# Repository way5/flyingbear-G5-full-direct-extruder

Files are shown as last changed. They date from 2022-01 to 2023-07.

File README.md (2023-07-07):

# FlyingBear Ghost 5: Direct Extruder
| WARNING | The project requires a minimal skills in electronics. Everything you do hereinafter is at your own risk. :) |
|:---:|:---|
| disclaimer | **Please refer to [issues](https://github.com/way5/flyingbear-G5-full-direct-extruder/issues) :beetle: if you have any suggestion or found an error.** |

## **+ Description**

**BOM:**

1. Carrige:
   -  BMG feeder by Mellow Store (right) - 1 pcs.
   -  NEMA17HS4023 motor - 1 pcs.
   -  Bolt M3 - 5 pcs.
   -  Nut M3 - 4 pcs.
   -  Screw M2 (PCB) - 3 pcs.
   -  Thru Threaded Inserts M3 - 5 pcs.
   -  Threaded Stud Bolt M3 - 4 pcs.
2. Y-axis Limit Switch:
   -  Bolt + Nut + Washer M2 - 1 pcs.
   -  Thru Threaded Insert M2 - 1 pcs.
   -  Any suitable Coil Spring (see photos) - 1 pcs.
3. Z-axis knob:
   - Bolt + Nut M3 - 1 pcs.
<br/>Optional:
   - Replacement coil spring (~5mm shorter than the stock one) - 1 pcs.
4. PCB:
   -  SMD LED diode - 1 pcs.
   -  SMD Resistor ≥ 1kOhm - 1 pcs.
   -  SMD Capacitor ~ 10nF - 1 pcs.
   -  Header Male 2x1 pins - 6 pcs.
   -  Header Male 7x2 pins - 1 pcs.

I'd recommend PETG or ABS plastic for all the printed parts. Keep in mind that it will be exposed to high heat near the hotend, espetially if you are using heated chamber on your printer.

The list of the parts you'd neet to print:

- Carrige
- Carrige Belt Clip
- Nozzle
- Y-axis Shaft Base + Pin Head
- Z-axis Nut + Nut Cap
- Back side cap for extruder motor insert

In case if you have installed heated chamber I strongly recommend you to prevent extruder motor overheat by using heatsinks and a cooling fan. I am using 30x30mm turbine that is attached to the carrige through the [extruder motor shroud](./OBJ/EXTRUDER%20MOTOR%20SHROUD.obj). See the corresponding 3d model.

Your new hotend carrige would look like this:

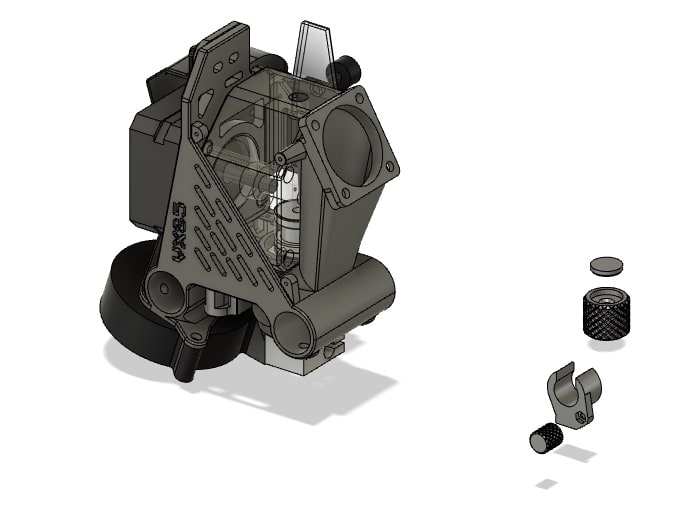
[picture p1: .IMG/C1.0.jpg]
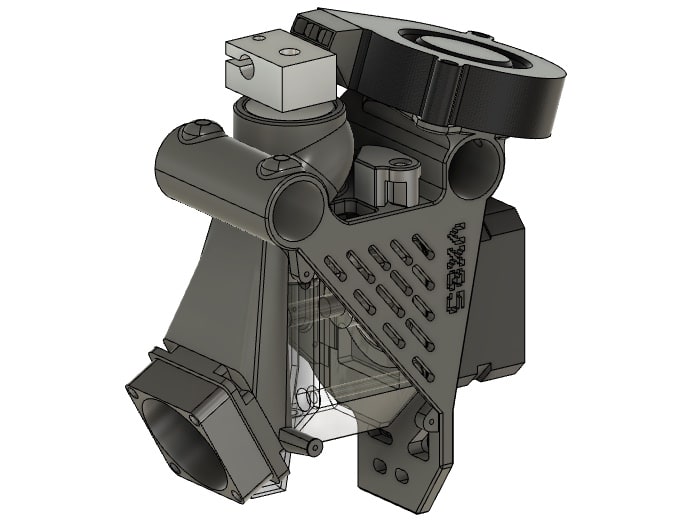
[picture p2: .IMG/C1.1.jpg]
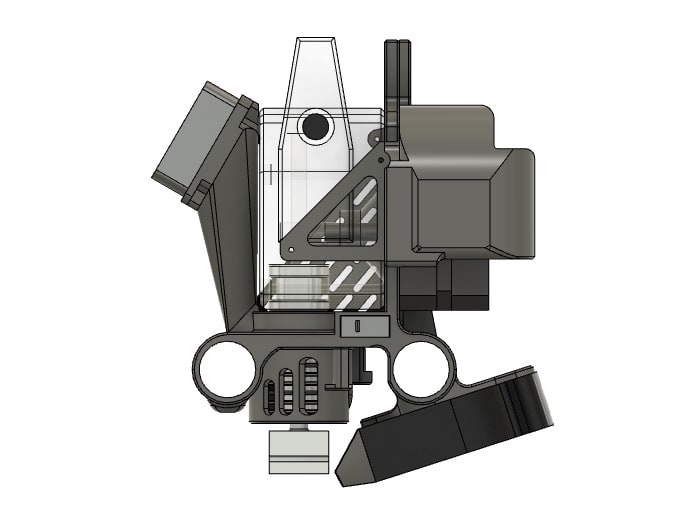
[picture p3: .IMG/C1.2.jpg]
||||
| --- | --- | --- |

For the extruder heatsink cooling being used stock Flyingbear's 30x30mm fan that is electrically connected (in parallel) to the same female pin header with extruder motor fan. Hotend cooling fan sits on the top of the air duct sleeve and blows downwards to the heatsink, see image below.

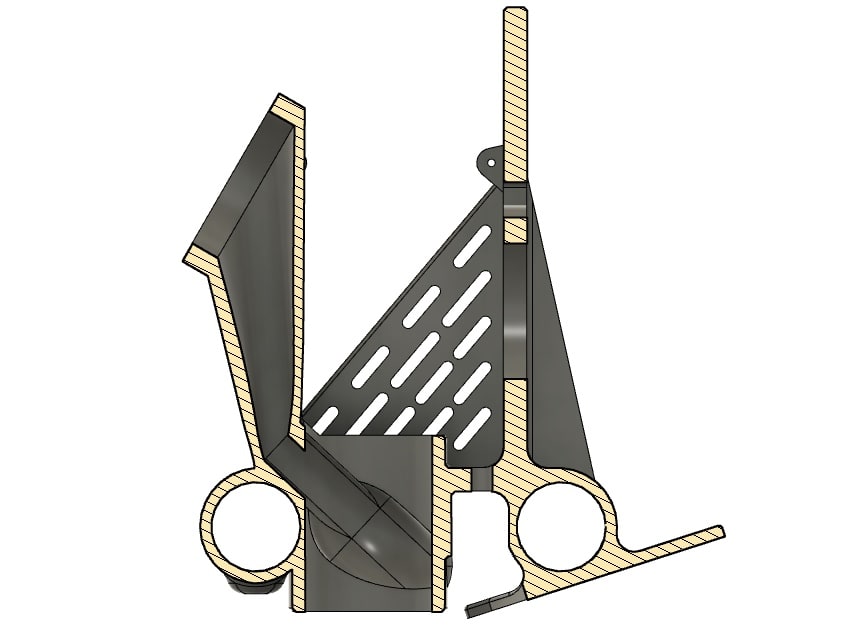
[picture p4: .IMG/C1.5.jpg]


You also would need to replace the standard PCB with following. You can make it yourself using etching method or using CNC if you have one. However I'd not recommend you to order a PCBs for now, because yet there are things to adjust or maybe to change.

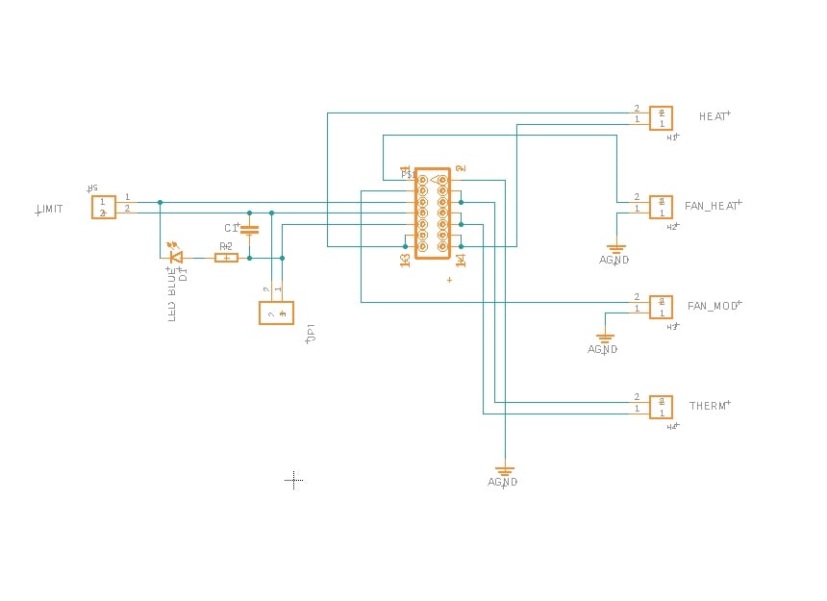
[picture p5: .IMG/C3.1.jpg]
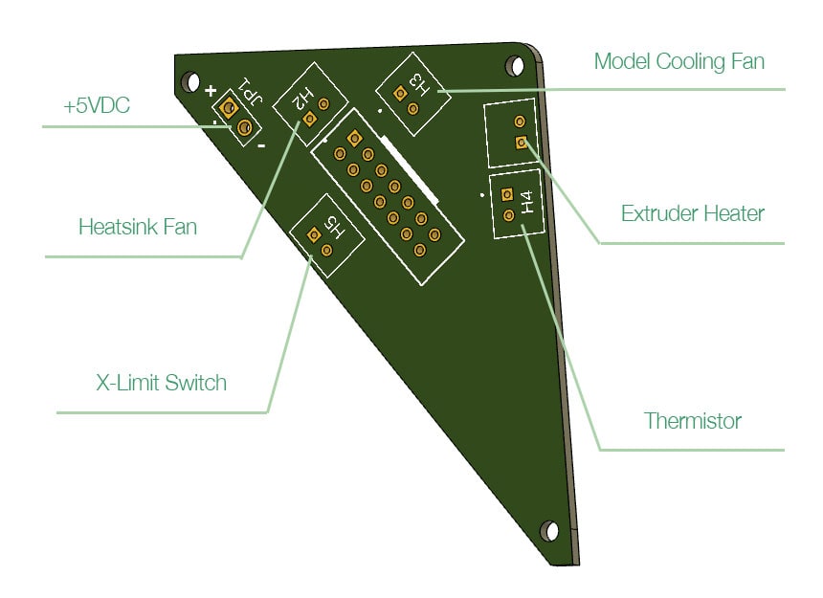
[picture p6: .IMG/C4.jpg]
|||
|:---:|:---:|

You might like to use a cable chain with your new extruder, so here it is. See [cable chain 1](OBJ/CABLE%20CHAIN%20LINK.obj), [cable chain 2](OBJ/CABLE%20CHAIN%20TERMLK.obj) and [cable chain 3](OBJ/CABLE%20CHAIN%20LOCK.obj).

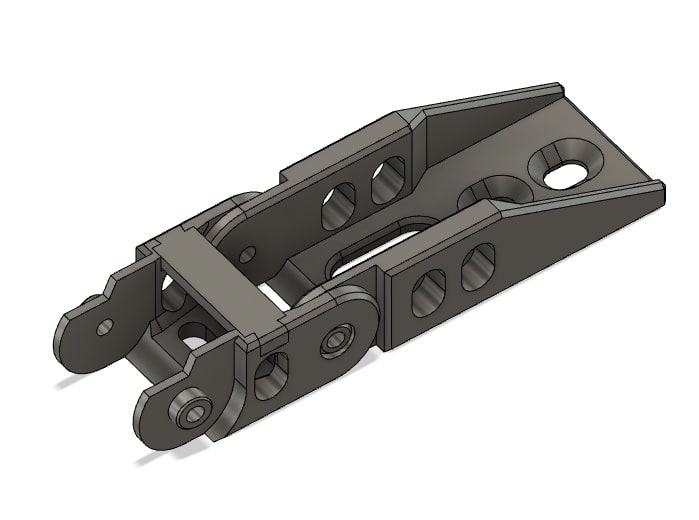
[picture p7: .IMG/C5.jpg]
cable chain


In addition you need to do a few more mods since home limit switches now are not reachable for the carriges. Linear bearings on the heated bed should be turned upside down, Z-axis limit switch assembly moves 10mm up (see product assembly) and an extension pin added on Y-axis carrige (see product assembly).
Also remove the X-axis limit switch bolt, you'll no longer need it.

The opposit side of the cable chain connects to the cable holder standoff. Those may be also used to install top side lights, though this is optional.

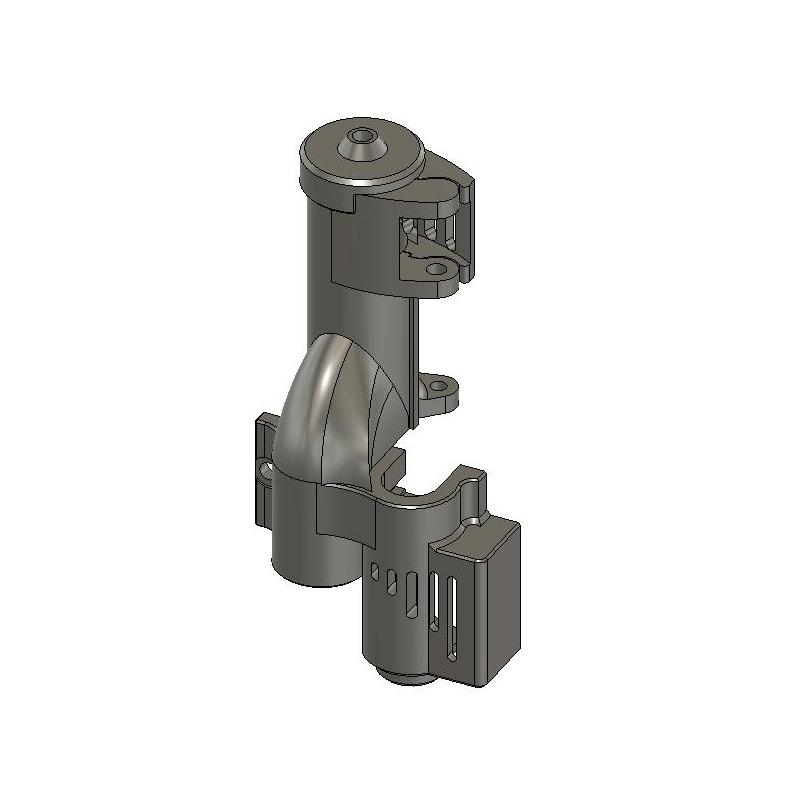
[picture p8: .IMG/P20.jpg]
cable standoff


At last you need to make changes in your printer firmware config. Change the maximum coordinate parameters as follows:

```

>X_MIN_POS 0
>Y_MIN_POS 0
>Z_MIN_POS 0
>X_MAX_POS 254
>Y_MAX_POS 195
>Z_MAX_POS 210

```

You can still adjust maximum values +/- few millimeters.

## **+ Final product view and assembled weights**

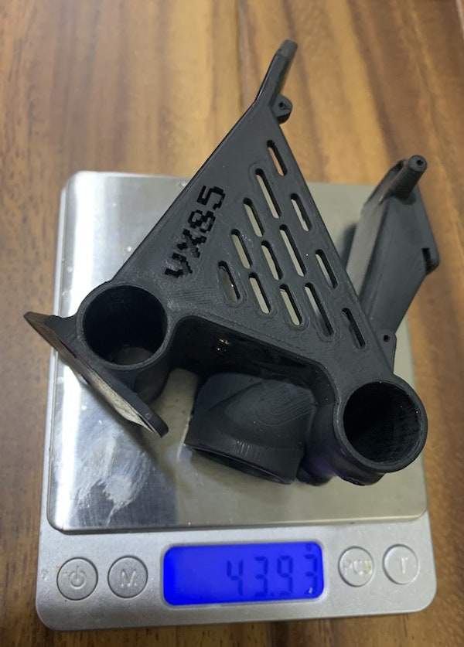
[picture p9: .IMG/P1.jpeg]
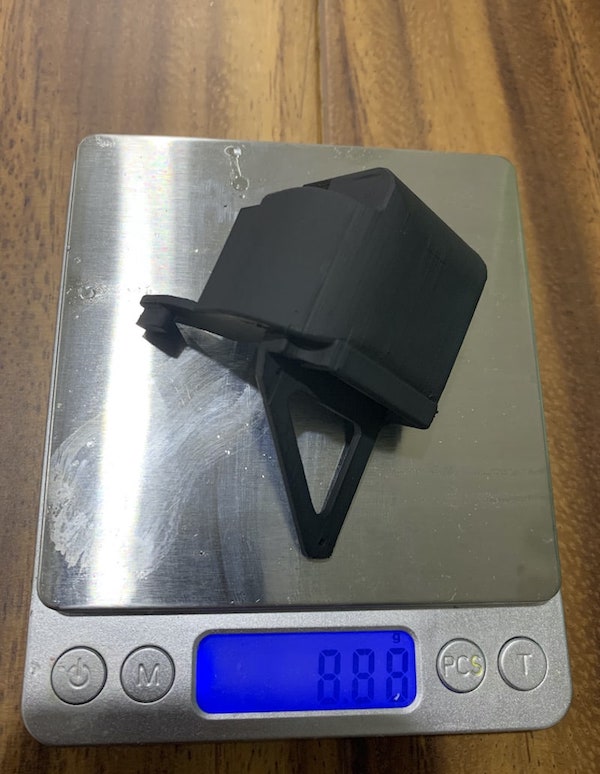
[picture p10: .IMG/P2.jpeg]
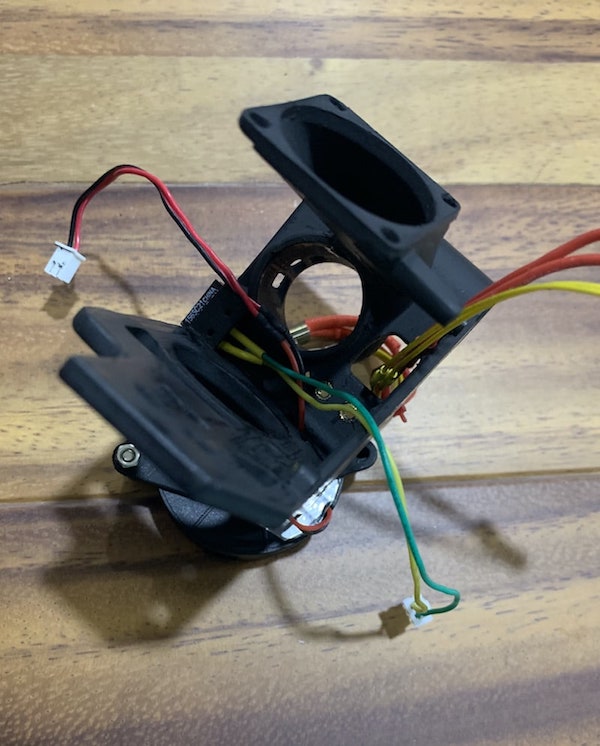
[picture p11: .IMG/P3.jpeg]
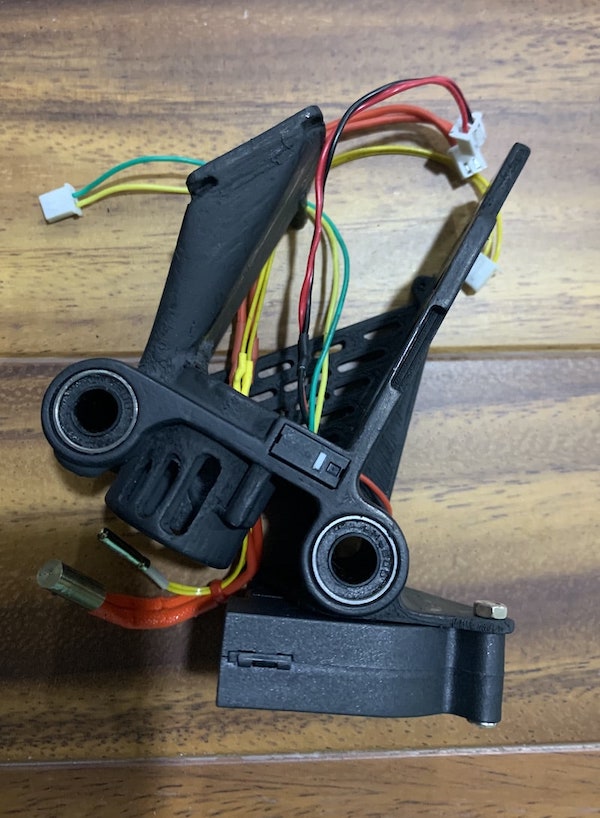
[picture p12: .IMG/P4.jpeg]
P4
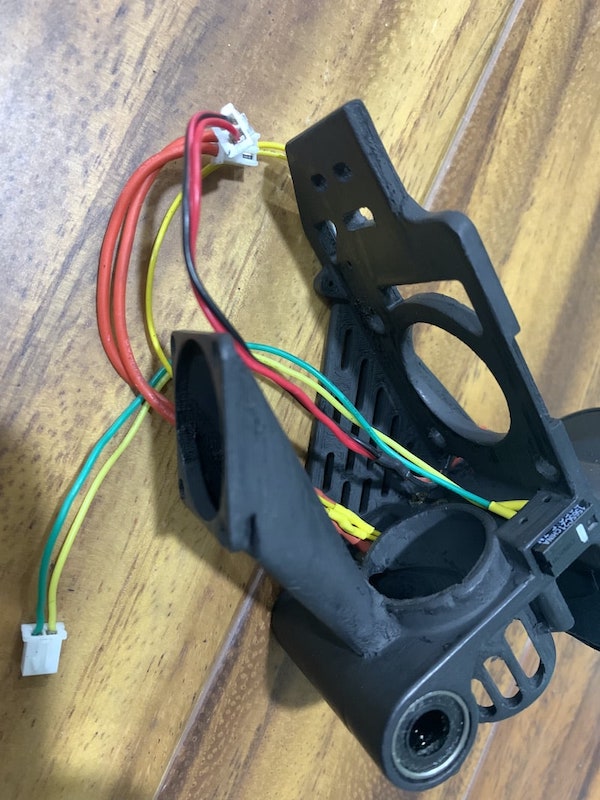
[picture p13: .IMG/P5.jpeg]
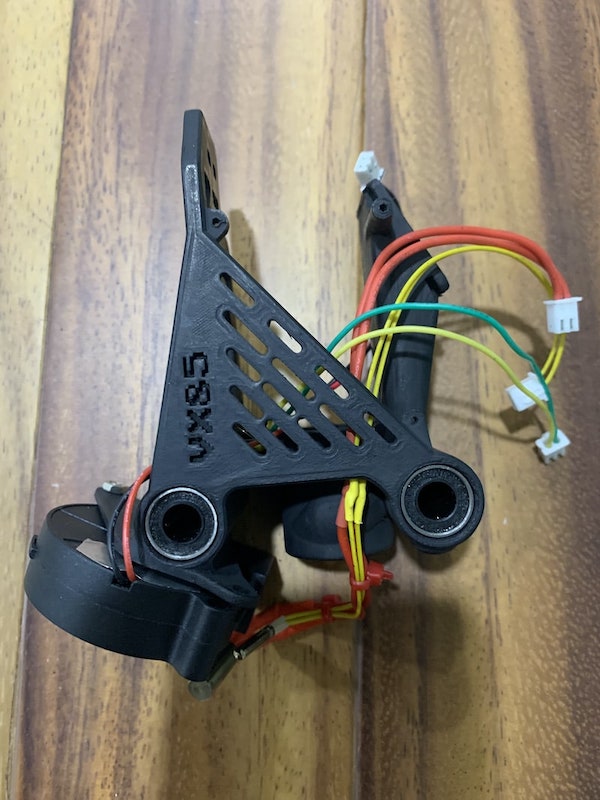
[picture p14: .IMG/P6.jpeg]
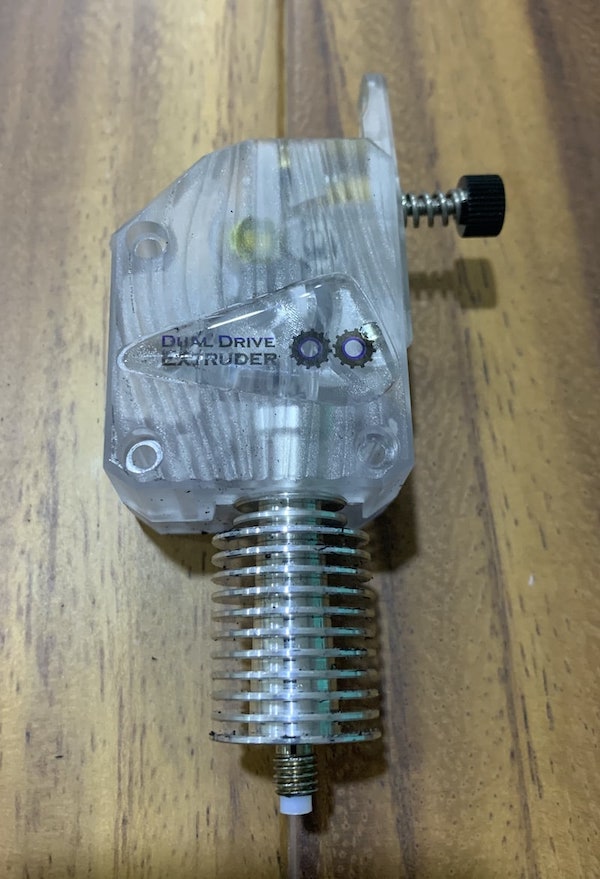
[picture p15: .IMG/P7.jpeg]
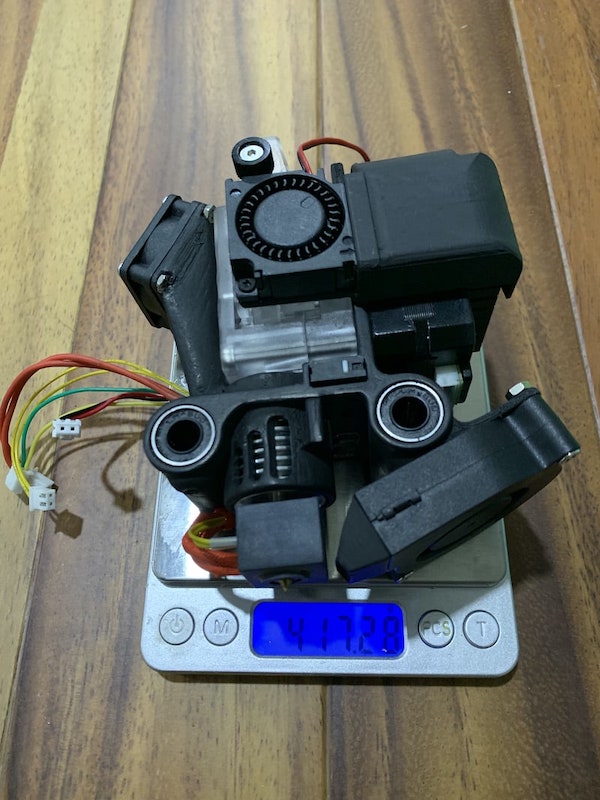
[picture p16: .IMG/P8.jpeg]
P8
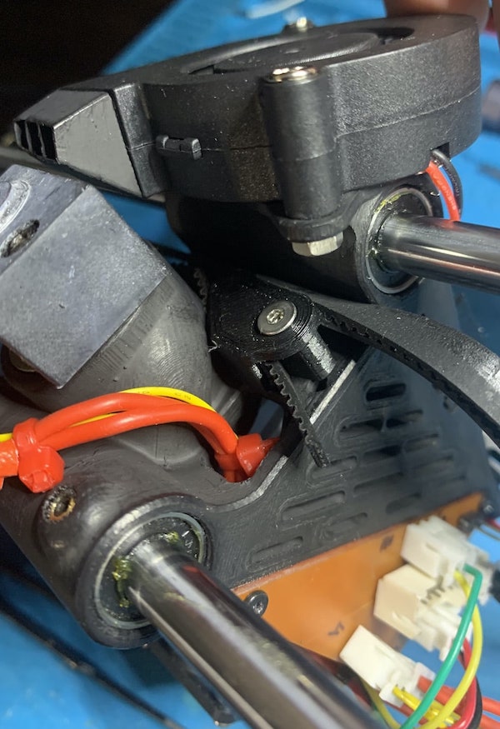
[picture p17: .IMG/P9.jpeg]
||||||||||
| --- | --- | --- | --- | --- | --- | --- | --- | --- |
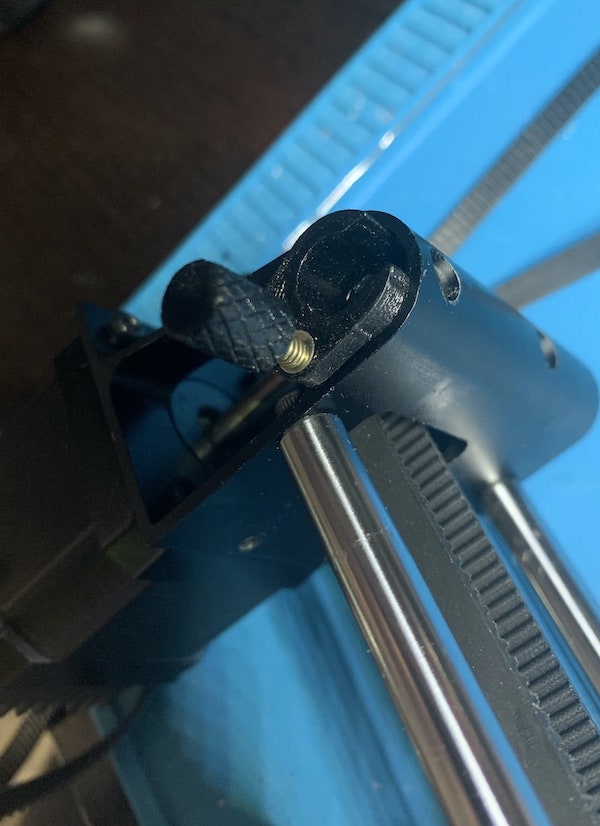
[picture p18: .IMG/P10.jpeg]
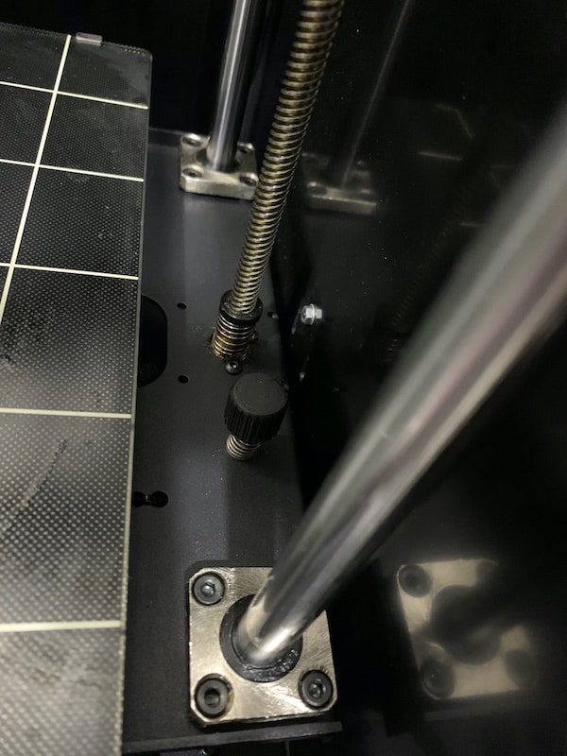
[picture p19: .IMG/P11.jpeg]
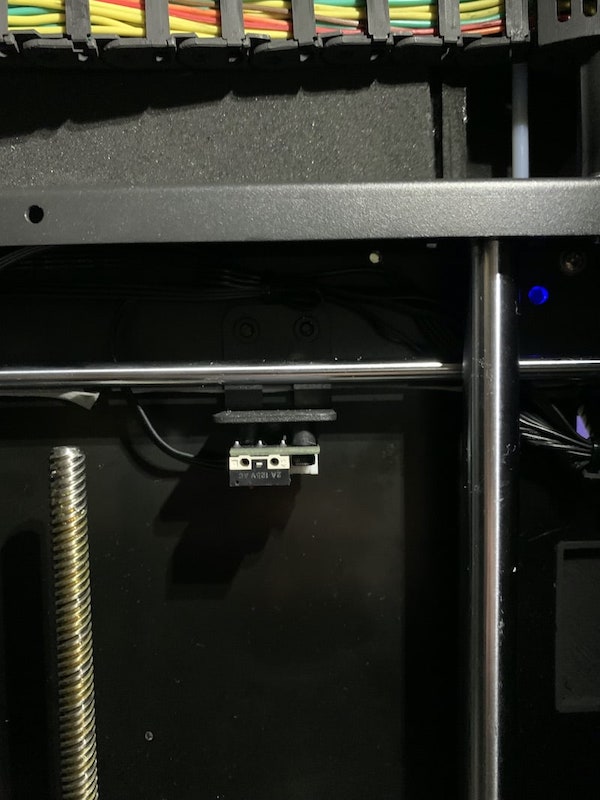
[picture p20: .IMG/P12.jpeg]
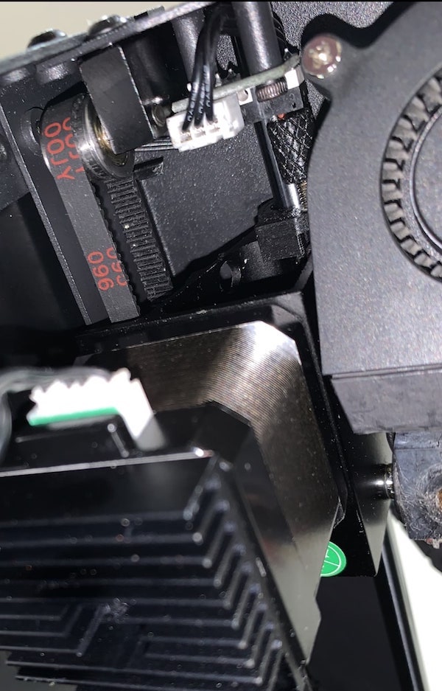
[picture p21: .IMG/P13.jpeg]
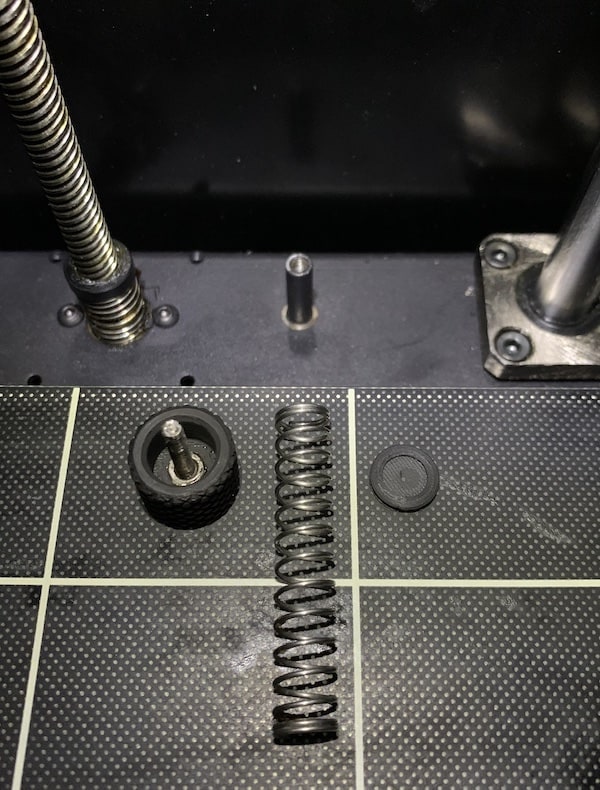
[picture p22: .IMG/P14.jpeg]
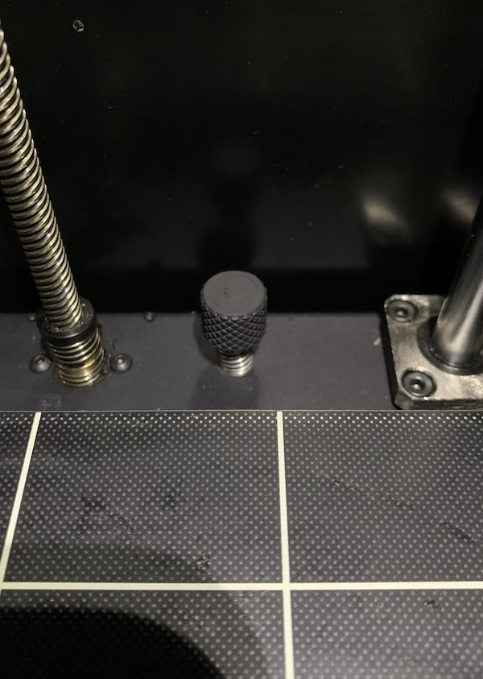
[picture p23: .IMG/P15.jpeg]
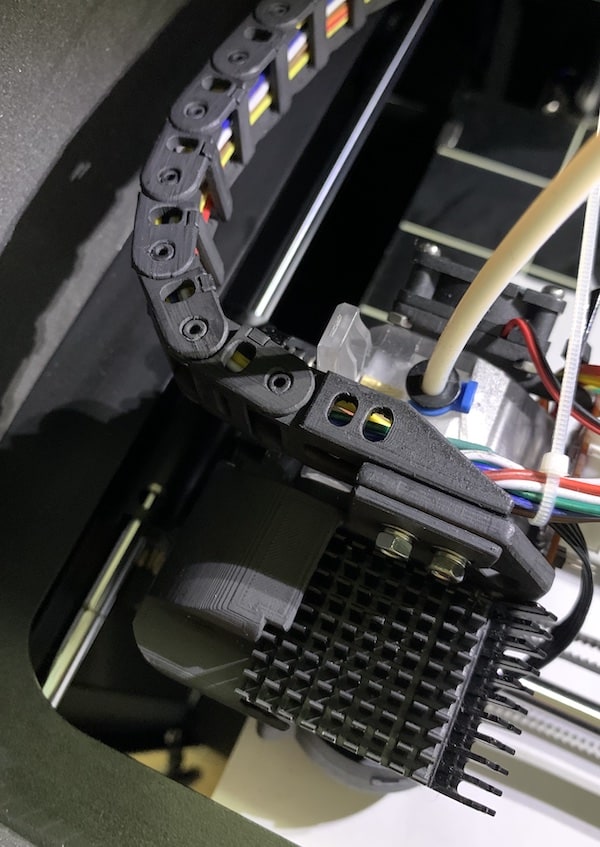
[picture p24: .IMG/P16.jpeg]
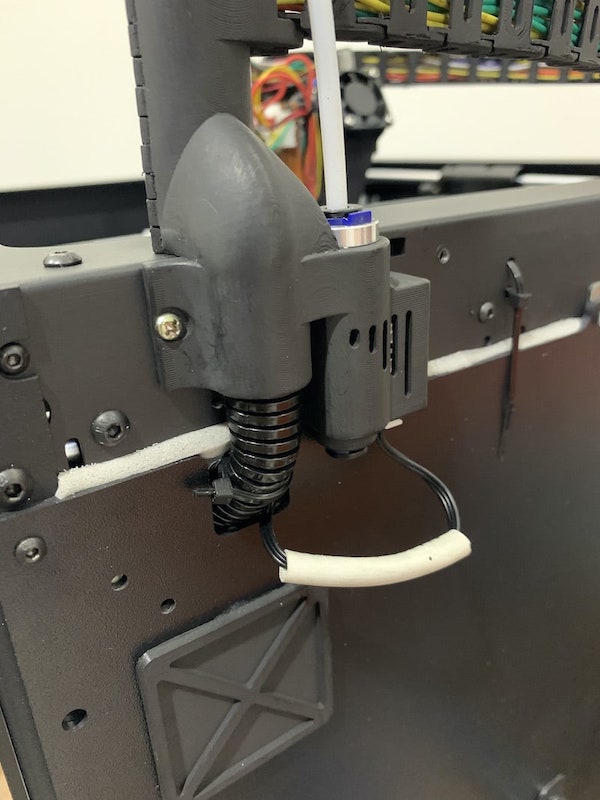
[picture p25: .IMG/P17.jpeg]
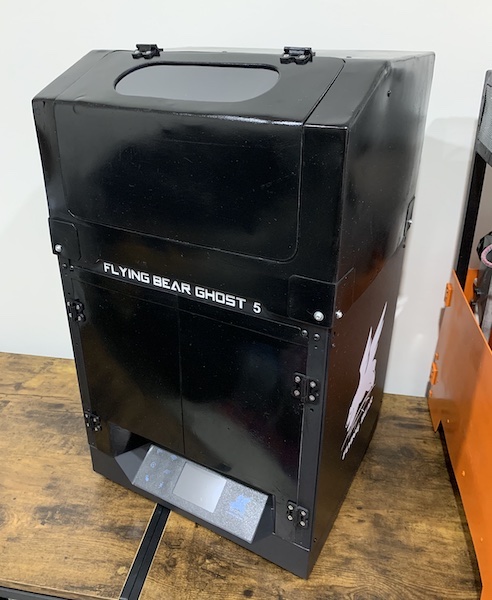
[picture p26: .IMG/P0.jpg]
FlyingBear Ghost 5 Heater Chamber
||||||||||||

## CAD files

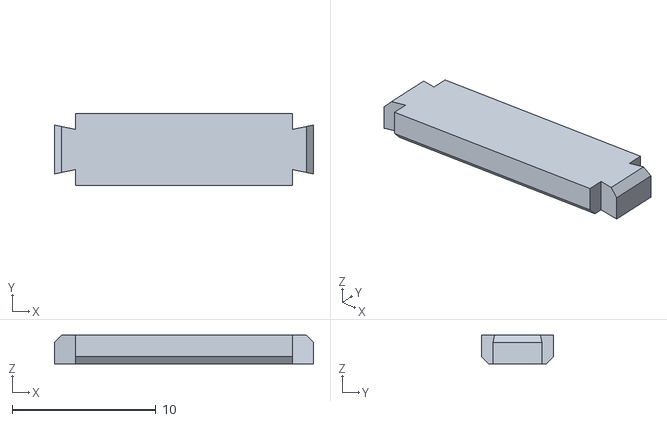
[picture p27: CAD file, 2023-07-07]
OBJ-STL/CABLE CHAIN LOCK.stl
18.0 x 5.00 x 2.00

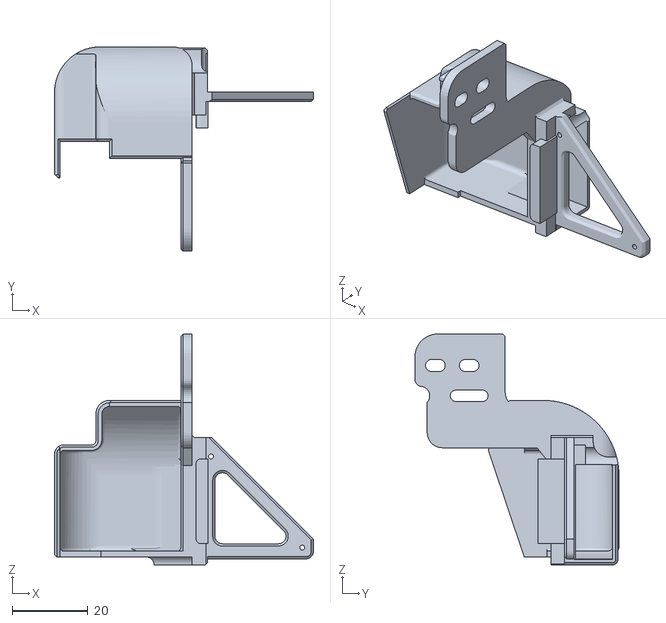
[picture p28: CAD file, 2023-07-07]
OBJ-STL/EXTRUDER MOTOR SHROUD.stl
68.3 x 53.8 x 60.9

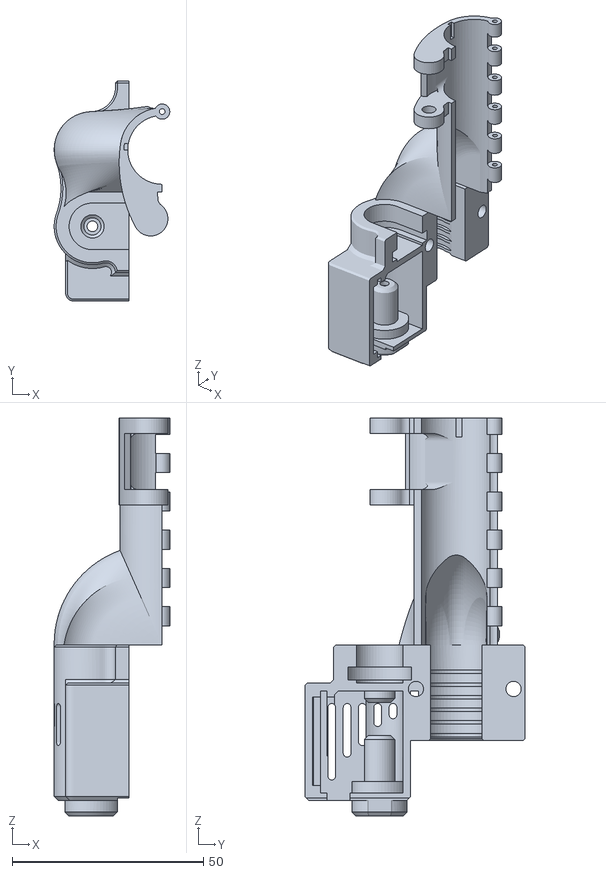
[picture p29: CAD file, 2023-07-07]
OBJ-STL/CABLE HOLDER STANDOFF BASE.stl
30.2 x 57.5 x 104.0

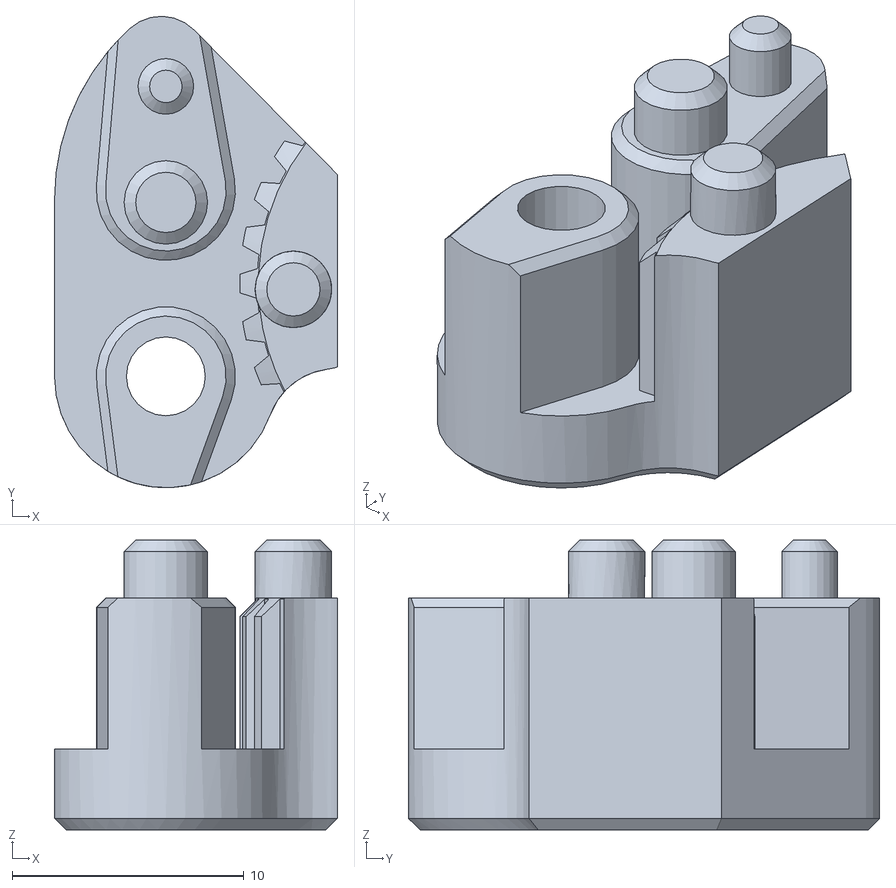
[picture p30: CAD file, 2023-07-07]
OBJ-STL/TIMING BELT CLIP.stl
12.2 x 20.3 x 12.5

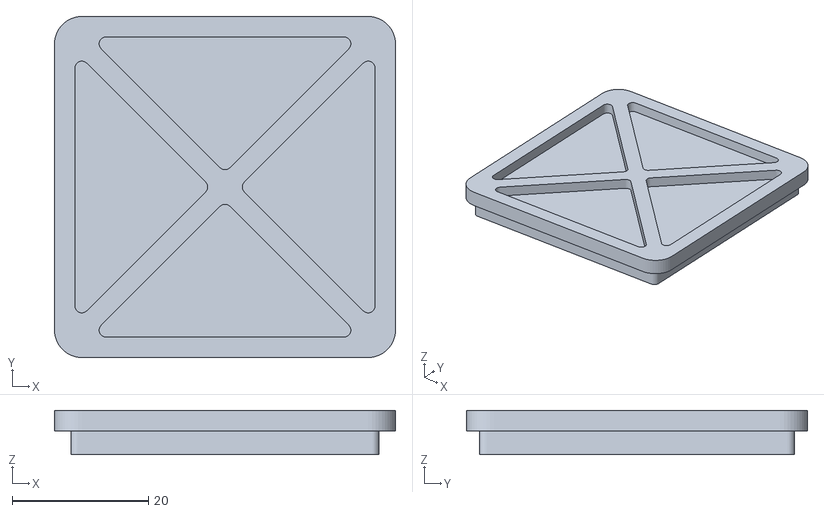
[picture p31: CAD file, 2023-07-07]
OBJ-STL/REAR HOLE CAP.stl
50.0 x 50.0 x 6.50

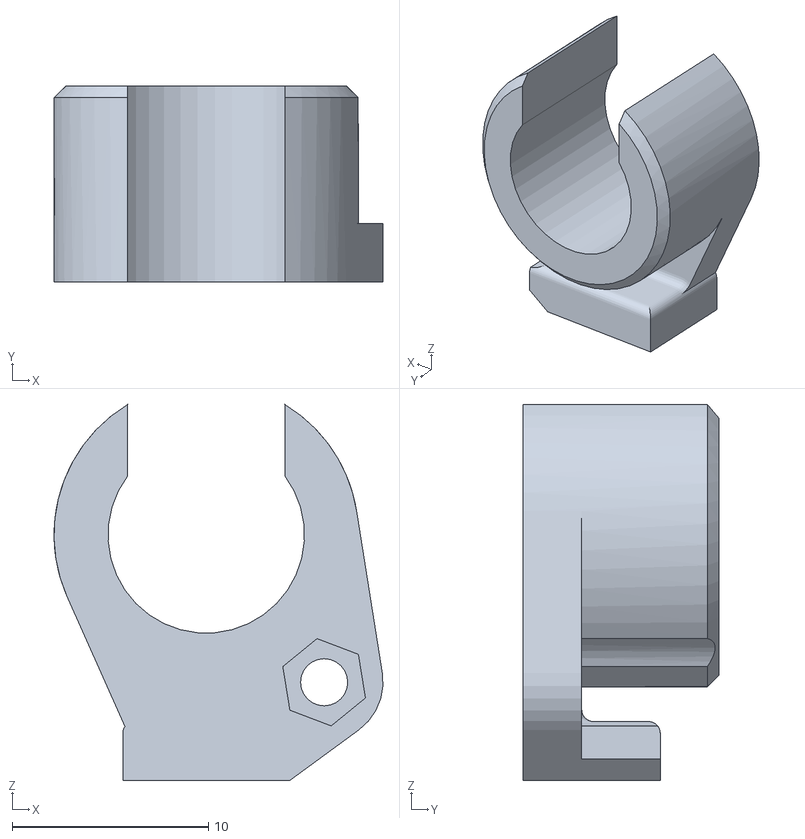
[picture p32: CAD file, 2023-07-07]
OBJ-STL/Y SHAFT BASE.stl
16.7 x 10.0 x 19.1

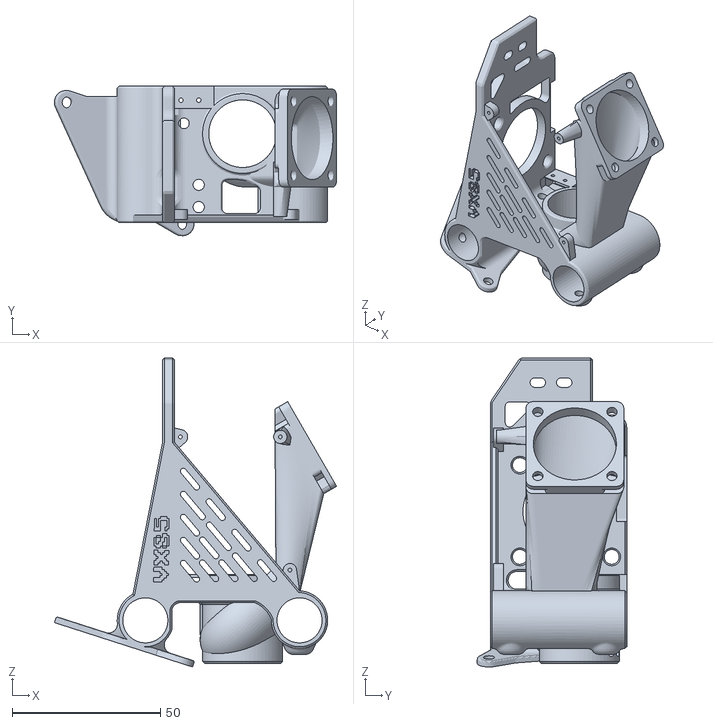
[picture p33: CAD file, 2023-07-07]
OBJ-STL/CARRIGE.stl
95.2 x 50.4 x 104.2

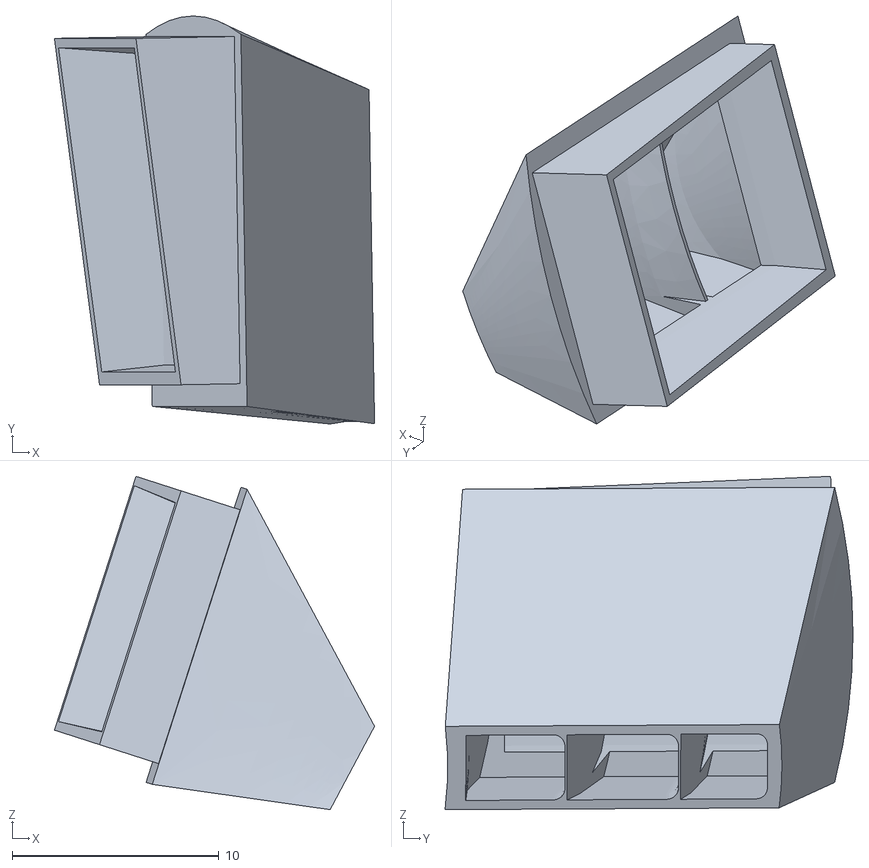
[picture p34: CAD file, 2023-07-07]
OBJ-STL/NOZZLE.stl
15.5 x 19.7 x 16.1

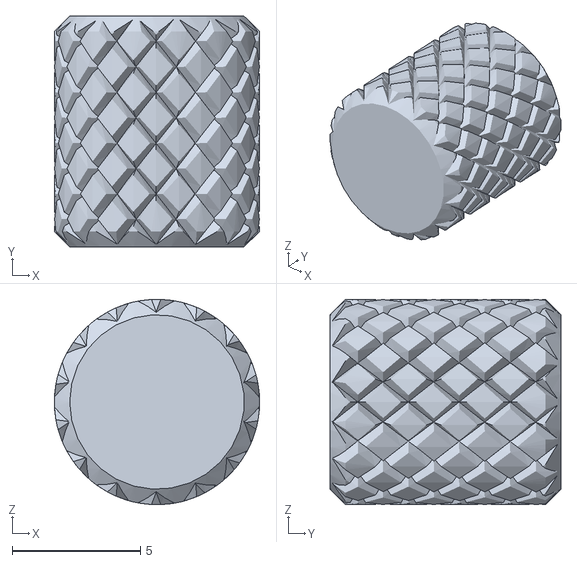
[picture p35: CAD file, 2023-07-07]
OBJ-STL/Y SHAFT PIN.stl
8.00 x 9.00 x 8.00

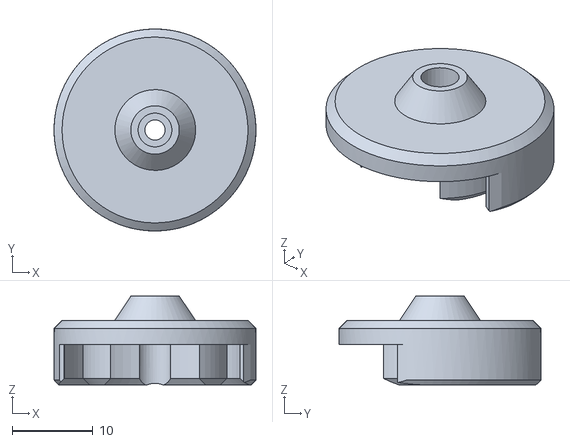
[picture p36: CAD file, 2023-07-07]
OBJ-STL/CABLE HOLDER STANDOFF PLUG.stl
25.0 x 25.0 x 11.0

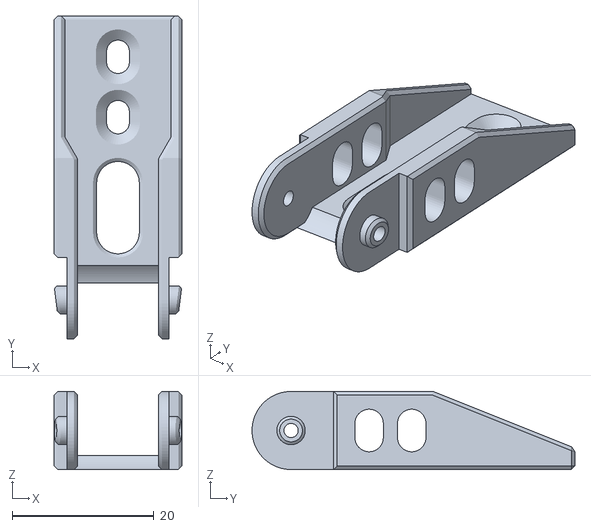
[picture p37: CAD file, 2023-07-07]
OBJ-STL/CABLE CHAIN TERMLK.stl
18.0 x 45.5 x 11.0

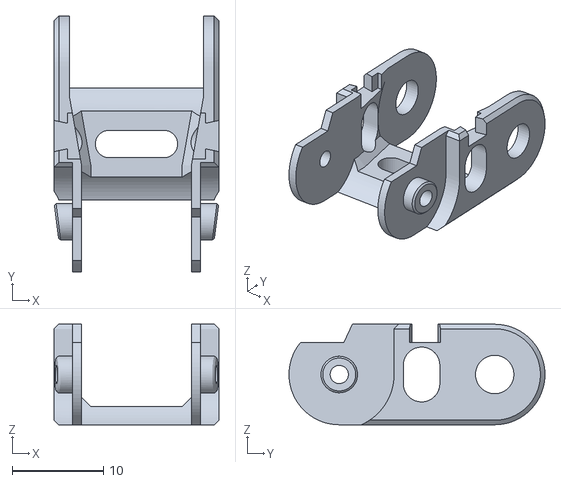
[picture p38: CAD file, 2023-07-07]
OBJ-STL/CABLE CHAIN LINK.stl
18.0 x 28.0 x 11.0

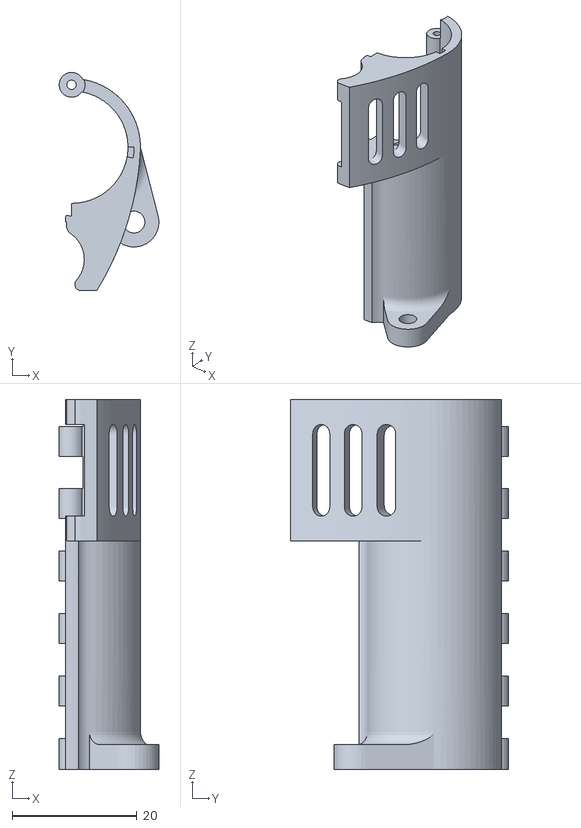
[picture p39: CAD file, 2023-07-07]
OBJ-STL/CABLE HOLDER STANDOFF LID.stl
16.0 x 35.0 x 59.3

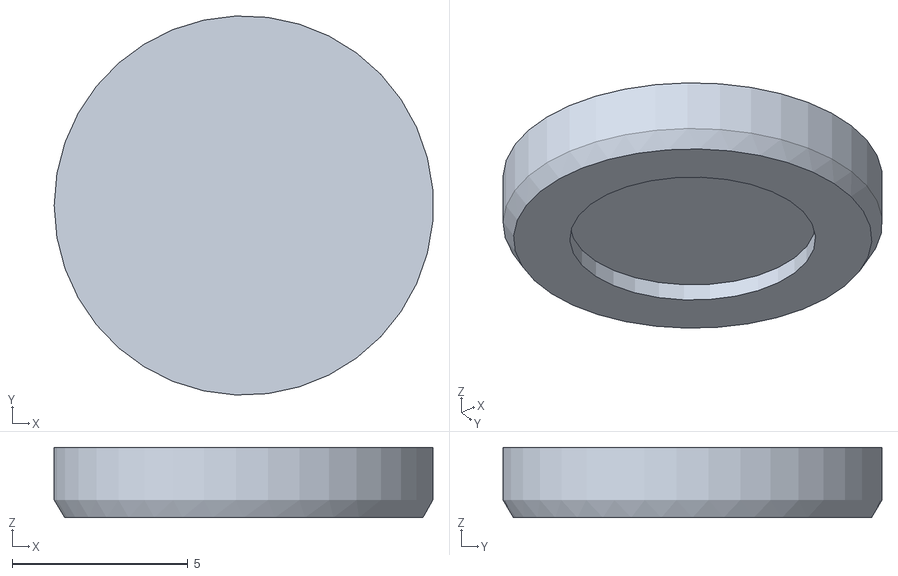
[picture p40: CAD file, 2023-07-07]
OBJ-STL/Z PIN NUT CAP.stl
10.8 x 10.8 x 2.00

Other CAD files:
OBJ-STL/Z PIN NUT.stl
OBJ-STL/CABLE CHAIN LINK.obj
OBJ-STL/CABLE CHAIN LOCK.obj
OBJ-STL/CABLE CHAIN TERMLK.obj
OBJ-STL/CARRIGE.obj
OBJ-STL/EXTRUDER MOTOR SHROUD.obj
OBJ-STL/NOZZLE.obj
OBJ-STL/REAR HOLE CAP.obj
OBJ-STL/TIMING BELT CLIP.obj
OBJ-STL/Y SHAFT BASE.obj
OBJ-STL/Y SHAFT PIN.obj
OBJ-STL/Z PIN NUT CAP.obj
OBJ-STL/Z PIN NUT.obj

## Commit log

2021-12-15 Update 1, Fixes: Carrige, Shroud, Belt Clip
2023-07-07 '23 up
    [CABLE CHAIN LINK.obj, CABLE CHAIN LINK.stl, CABLE CHAIN LOCK.obj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]
